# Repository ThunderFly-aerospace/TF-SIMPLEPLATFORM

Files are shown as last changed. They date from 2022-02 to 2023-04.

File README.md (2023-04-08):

# TF-SIMPLEPLATFORM - UAV autogyro takeoff platform

Device for launching unmanned drones (especialy autogyro type) from moving platforms (e.g. automobile roof).

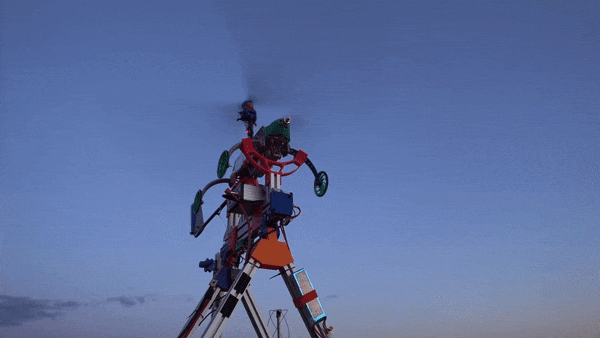
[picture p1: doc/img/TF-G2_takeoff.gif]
TF-SIMPLEPLATFORM with TF-G2 takeoff


The TF-SIMPLEPLATFORM is designed for launching of the unmanned [autogyro TF-G2](https://github.com/ThunderFly-aerospace/TF-G2/). Thanks to the combination of the this starting platform and the automatic takeoff mode of the TF-G2 unmanned autogyro, it is possible to perform safe and almost unattended takeoff. Platform is controlled from GCS based on realtime data from the UAV trough data-link. The platform can be disconnected manually (by operator) due to service operations.

The goal of the platform and automatic takeoff solution is to maximize the simplicity of the takeoff process and protect drone operators from external influences, such as adverse weather conditions.

## Parameters

| Parameter | Value | Note |
|---|---|---|
| Platform type | Rigid mount | Aluminium profiles design |
| Actuator| Clamps | |
| Manual override | Button on platform | |
| Remote control interface | USB/RS232 | |
| Operator takeoff confirmation | Yes, remote button | Wired controller |
| Control Software | Firmware, Mavlink interface in GCS | |
| Supported UAVs | [ThunderFly TF-G2](https://github.com/ThunderFly-aerospace/TF-G2) | |
| Supported flight stack | PX4 | (MavLink protcol) |

## Clamps mount mechanism
ezgif com-gif-maker

## Usage
  1. Prepare all required equipment. Check if it is properly mounted and connected. 
  1. ARM the autogyro, check all avionics. 
  2. Push the trigger switch to releas rotor holder. 
  3. Run by car few tens of meters
  4. Autogyro will takeoff automatically from roof. 

### Installation
The first step is to assemble the platform onto the movable platform. The standard method of assembly involves inserting it into plastic parts and securing it with a screw. It is important to tight the screw with the correct torque to prevent spontaneous loosening of the screw. 

### Wiring 
After mounting the platform, it is necessary to correctly connect it. The outdoor part is connected with the inner box using a cable terminated on both ends with the same 12-pin connector. This cable provides both power and data communication for the platform. 

## Description of control elements
The platform is equipped with a variety of actuators, sensors, control elements and visualization components. 

### Actuators
 - Servo motor for rotor holder
 - Servo motor for clamp

### Sensors 
 - Sensor of drone presence (in future version)

### Control elements
 - Button on platform itself - Restart button
 - Botton on platform itself - Open clamp
 - Button on wired controller - Permission for takeoff
 - External input for breake signal

### Visualization elements
 - 2 LEDS on platform (Platform status) 
 - 1 Loud buzzer on platform (Release status)
 - 2 LEDS on wired controller (Platform status)
 - 1 Buzzen on wired controller (Release status)

### Platform control 
The platform is typically controlled from a ground-station via USB or RS232. The platform is connected to the ground control station either through the USB port from internal box of the platform or directly through RS232. Once properly connected, it should be possible to communicate with the platform via a serial interface.

The ground stations from ThunderFly company are equipped with [software](https://github.com/ThunderFly-aerospace/TF-R1/blob/master/scripts/release_platform/release_platform_serial.py) that is capable of controlling the platform based on data obtained from the drone through the MAVLink network.

## Technical images 
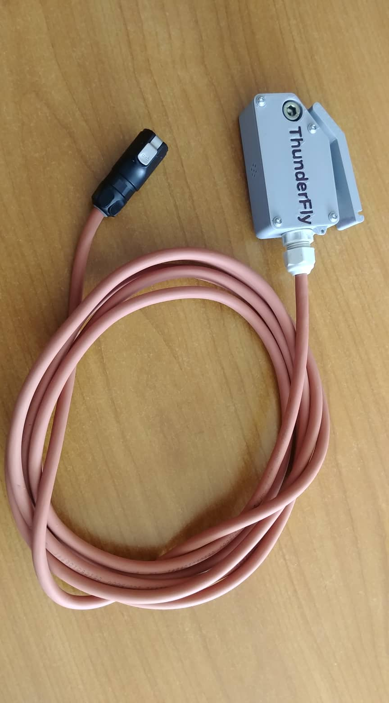
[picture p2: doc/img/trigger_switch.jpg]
TF-SIMPLEPLATFORM trigger switch

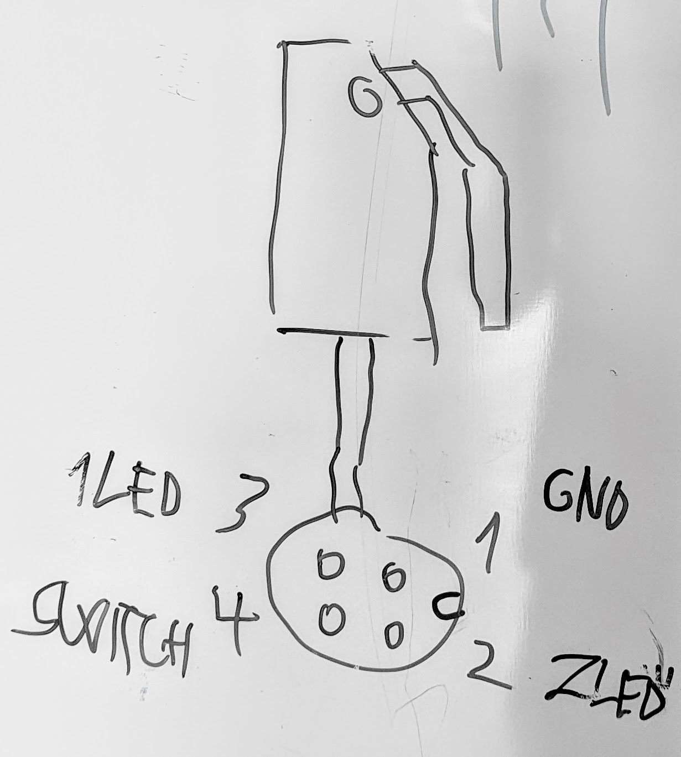
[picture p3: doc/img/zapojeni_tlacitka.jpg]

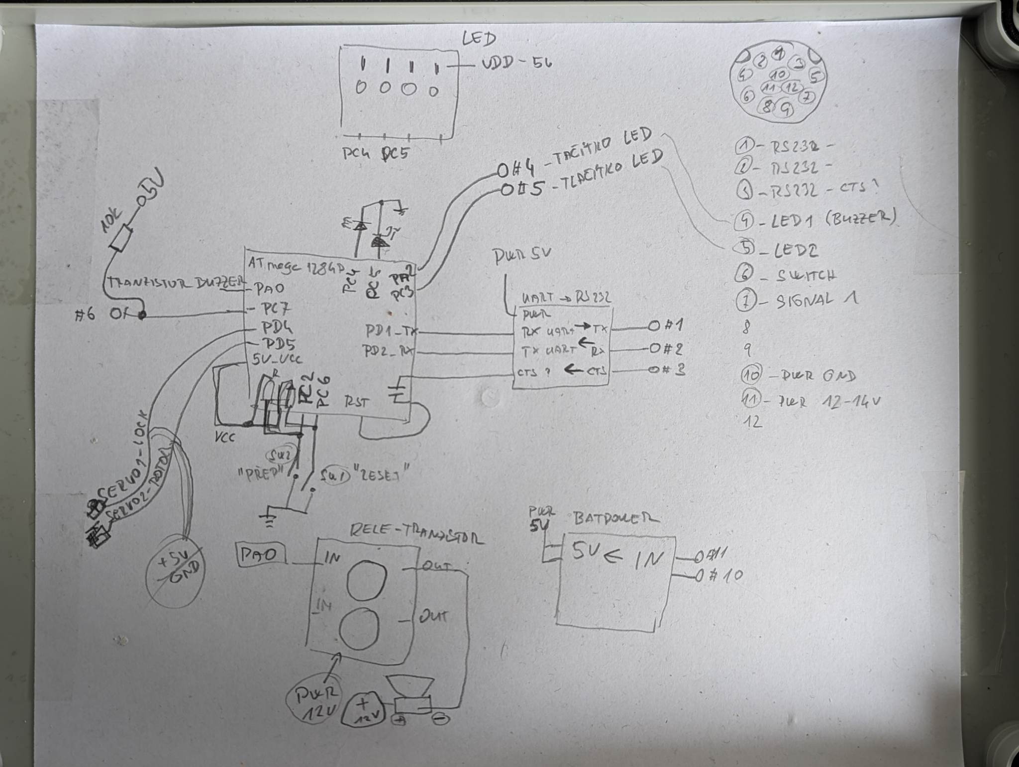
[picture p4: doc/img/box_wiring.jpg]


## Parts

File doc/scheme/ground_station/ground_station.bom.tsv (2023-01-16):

Id | Description | Qty | Unit | Designators
1 | Cable, 2 wires | 0 | m
2 | Cable, 3 wires | 0 | m
3 | Cable, 4 wires | 0 | m
4 | Connector, 20A | 1 |  | Power_Connector
5 | Connector, Ground Station Power | 1 |  | Main_Power
6 | Connector, MLAB RS232SINGLE01A | 1 |  | RS232
7 | Connector, MLAB USB232R02A | 1 |  | USB
8 | Connector, USB-A | 1 |  | MOX

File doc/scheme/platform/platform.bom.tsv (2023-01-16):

Id | Description | Qty | Unit | Designators
1 | Cable, 10 wires | 0 | m
2 | Cable, 2 wires | 0 | m
3 | Cable, 8 wires | 0 | m
4 | Cable, 9 wires | 0 | m
5 | Connector | 4 |  | Confirm_Btn_Connector, Platform_LED_1, Platform_LED_2, Servo_Connector
6 | Connector, 20A | 1 |  | Power_Connector
7 | Connector, GQ12B-10/R/A | 2 |  | Reset_Button, Rotor_Button
8 | Connector, MLAB ATmegaTQ4401A | 1 |  | Arduino
9 | Connector, MLAB BATPOWER04C | 1 |  | Power_Module
10 | Connector, MLAB NFET4X01B | 1 |  | NFET
11 | Connector, MLAB RS232SINGLE01A | 1 |  | RS232
12 | Connector, SC235 AF | 1 |  | Buzzer

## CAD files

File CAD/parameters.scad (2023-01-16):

maximum_printable_size = 150;

layer_thickness = 0.3;
global_clearance = 0.5;


//Screw diameter and nut for M10 [mm]
M10_screw_diameter = 10.4;
M10_head_height = 10;
M10_head_diameter = 16+0.5;
M10_nut_height = 10.5;
M10_nut_diameter = 25.5;
M10_nut_pocket = 22.3;

//Screw diameter for M8 [mm]
M8_screw_diameter = 8.6;
M8_head_height = 8;
M8_head_diameter = 13.5;
M8_nut_height = 7.5;
M8_square_nut_thin_height = 4.5;
M8_nut_diameter = 14.4 + 0.5;
M8_nut_pocket = 13 + 0.5;
M8_washer_diameter = 16;
M8_washer_thickness = 1.5;


//Screw diameter and nut for M6 [mm]
M6_screw_diameter=6.5;
M6_head_diameter = 10+0.5;
M6_head_height = 6;
M6_nut_height = 4.9;
M6_nut_diameter = 11.8;
M6_nut_pocket = 10.4;
M6_square_nut_height = 3;
M6_square_nut_diameter = 10;
M6_washer_thickness = 1.6;

//Screw diameter and nut for M5 [mm]
M5_screw_diameter=5.5;
M5_head_height = 5;
M5_head_diameter = 13+0.5;
M5_nut_height = 4.5;
M5_nut_diameter = 9.4;
M5_nut_pocket = 8.4;

//Screw diameter and nut for M4 [mm]
M4_screw_diameter=4.5;
M4_screw_head_height = 4;
M4_nut_height = 3.2;
M4_nut_diameter = 8.4;
M4_nut_pocket = 7.5;

//Screw diameter and nut for M3 [mm]
M3_screw_diameter = 3.2;
M3_nut_height = 2.7;
M3_nut_diameter = 6.6;
M3_nut_pocket = 5.6;
M3_screw_head_height = 3;

//Screw diameter and nut for M2,5 [mm]
M2_5_screw_diameter = 2.7;
M2_5_nut_height = 2.3;
M2_5_nut_diameter = 6;
M2_5_nut_pocket = 5.5;

//ALU profile
ALU_profile_width = 30.5;
ALU_profile_holder_wall_thickness = 3;
ALU_profile_groove_width = 8;





// Platform parameters ////////////////////////////////////////////
// Main profile parameters
starting_platform_length = 1000; // Main platform profile length
starting_platform_angle = 10; // Angle of attack for platform

// Main cube profile lengths
profile_length_x = 600;
profile_length_y = 600;
profile_length_z = 260;


// Compressor dimensions
compressor_length_x = 410;
compressor_length_y = 140;
compressor_length_z = 310;

// Platform front support parameters
front_holder_width = 160;
front_holder_angle = 25;
front_holder_height = 60;
front_holder_offset = 15;
front_holder_height_offset = 110;

// Lock moving servo parameters
// static par.
servo_length = 40;
servo_width = 20;
servo_height = 40;
servo_axle_offset = 12.5;
servo_axle_height = 5;
servo_movement_angle = 60;
servo_movement_angle_offset = -35; // angle offset up
servo_force = 1.65; // [N/m] torque of servo

// dynamic par.
servo_arm_length = servo_width/2+ALU_profile_width/2+ALU_profile_holder_wall_thickness+4;
servo_travel_y = cos((servo_movement_angle-abs(servo_movement_angle_offset))/2)*servo_arm_length;
servo_arm_hole_length = (servo_arm_length/cos(servo_movement_angle/2))-servo_arm_length+M3_screw_diameter;
servo_joint_offset = sin(servo_movement_angle+servo_movement_angle_offset)*(servo_arm_length+servo_arm_hole_length)+servo_axle_offset;
servo_joint_offset_by_angle = -tan(servo_movement_angle_offset)*servo_arm_length;
servo_max_linear_force = servo_force/(servo_arm_length/1000); // max servo linear force [N]
servo_min_linear_force = cos(servo_movement_angle+abs(servo_movement_angle_offset))*servo_max_linear_force; // min servo linear force [N] in the most extreme position
servo_holding_linear_force = cos(servo_movement_angle+servo_movement_angle_offset)*servo_max_linear_force; // min servo linear force [N] in holding position

// Lock static parameters
lock_screws_dia = 3.2;
lock_depth = 20;
lock_axle_diameter = 15;
lock_grab_axle_dia = 13;
lock_arms_joint_offset = 30;
lock_arms_joint_angle = 90-.01;
lock_tooth_width = 2;

lock_tube_angle = 0;

// Lock dynamic parameters
lock_push_force = (servo_holding_linear_force/cos(lock_arms_joint_angle))/cos(lock_arms_joint_angle); // lock arm pushing force on linear servo joint
lock_push_arm_length = 45;
lock_arm_force_ratio = 1; // lock arm change holding force ratio (0.5 = arm will have half holding force)
lock_hold_arm_length = lock_push_arm_length/lock_arm_force_ratio;
lock_holding_force = lock_push_force*lock_arm_force_ratio;
lock_joint_arm_length = lock_push_arm_length;

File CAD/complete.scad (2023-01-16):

include <./parameters.scad>
use <./src/lib/ALU_profile.scad>

use <./src/888_1010.scad> // not used

use <./src/assembly/cube_box.scad>
use <./src/assembly/platform.scad>


// Measuring box
main_box();

// Platform
translate([-22, 0, profile_length_z-ALU_profile_width/2+2])
rotate([0, -starting_platform_angle, 180])
platform();

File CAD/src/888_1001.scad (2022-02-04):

include <../parameters.scad>
use <./lib/ALU_profile_holder_top.scad>



module 888_1001() {
	translate([0, 35.01, 0])
	difference() {
		union() {
			hull() {
				cube([ALU_profile_width+ALU_profile_holder_wall_thickness*2, 5, ALU_profile_width]);

				translate([ALU_profile_width+ALU_profile_holder_wall_thickness*2+8, 70, 0])
				cylinder(d=5, h=ALU_profile_width/2, $fn=30);

				translate([-8, 70, 0])
				cylinder(d=5, h=ALU_profile_width/2, $fn=30);
			}

			translate([0, -35.01, 0])
			ALU_profile_holder_top();
		}
		

		// tube hole
		translate([0, 0, -1])
		hull() {
			translate([ALU_profile_width/2+ALU_profile_holder_wall_thickness, 60, 0])
			cylinder(d=lock_grab_axle_dia, h=ALU_profile_width+2, $fn=30);

			translate([ALU_profile_width+ALU_profile_holder_wall_thickness*2+8, 80, 0])
			cylinder(d=lock_grab_axle_dia, h=ALU_profile_width+2, $fn=30);

			translate([-8, 80, 0])
			cylinder(d=lock_grab_axle_dia, h=ALU_profile_width+2, $fn=30);
		}

		// middle body hole
		translate([0, 0, -1])
		hull() {
			translate([ALU_profile_width/2+ALU_profile_holder_wall_thickness-8, 15, 0])
			cylinder(d=lock_grab_axle_dia, h=ALU_profile_width+2, $fn=30);

			translate([ALU_profile_width/2+ALU_profile_holder_wall_thickness-10, 15, 0])
			cylinder(d=lock_grab_axle_dia, h=ALU_profile_width+2, $fn=30);

			translate([ALU_profile_width/2+ALU_profile_holder_wall_thickness-8, 40, 0])
			cylinder(d=lock_grab_axle_dia, h=ALU_profile_width+2, $fn=30);

			translate([2, 50, 0])

			cylinder(d=lock_grab_axle_dia, h=ALU_profile_width+2, $fn=30);
		}

		mirror([1, 0, 0])
		translate([-ALU_profile_width-ALU_profile_holder_wall_thickness*2, 0, -1])
		hull() {
			translate([ALU_profile_width/2+ALU_profile_holder_wall_thickness-8, 15, 0])
			cylinder(d=lock_grab_axle_dia, h=ALU_profile_width+2, $fn=30);

			translate([ALU_profile_width/2+ALU_profile_holder_wall_thickness-10, 15, 0])
			cylinder(d=lock_grab_axle_dia, h=ALU_profile_width+2, $fn=30);

			translate([ALU_profile_width/2+ALU_profile_holder_wall_thickness-8, 40, 0])
			cylinder(d=lock_grab_axle_dia, h=ALU_profile_width+2, $fn=30);

			translate([2, 50, 0])
			cylinder(d=lock_grab_axle_dia, h=ALU_profile_width+2, $fn=30);
		}
	}
}

888_1001();

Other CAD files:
CAD/src/888_1002.scad
CAD/src/888_1003.scad
CAD/src/888_1004.scad
CAD/src/888_1005.scad
CAD/src/888_1006.scad
CAD/src/888_1007.scad
CAD/src/888_1008.scad
CAD/src/888_1009.scad
CAD/src/888_1010.scad
CAD/src/888_1011.scad
CAD/src/888_1012.scad
CAD/src/888_1013.scad
CAD/src/888_1014.scad
CAD/src/888_1015.scad
CAD/src/888_1016.scad
CAD/src/888_2001.scad
CAD/src/888_2002.scad
CAD/src/888_2003.scad
CAD/src/888_2004.scad
CAD/src/888_2005.scad
CAD/src/888_3001.scad
CAD/src/888_3002.scad
CAD/src/888_3003.scad
CAD/src/888_3004.scad
CAD/src/888_3005.scad
CAD/src/888_3006.scad
CAD/src/888_3007.scad
CAD/src/assembly/cube_box.scad
CAD/src/assembly/front_support.scad
CAD/src/assembly/lock.scad
CAD/src/assembly/platform.scad
CAD/src/assembly/rotor_lock.scad
CAD/src/printplate/888_1001_printplate.scad
CAD/src/printplate/888_1002_printplate.scad
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

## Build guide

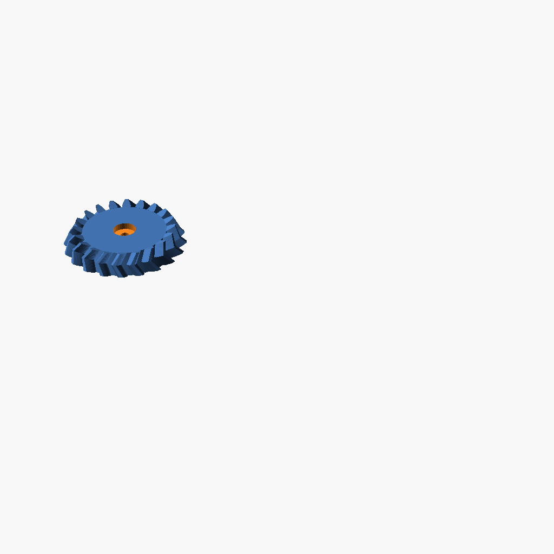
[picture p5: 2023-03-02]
CAD/png/888_3003_printplate.png

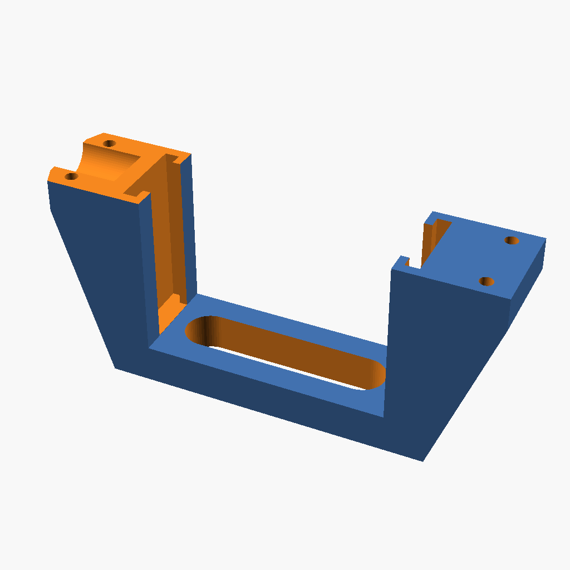
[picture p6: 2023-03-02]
CAD/png/888_3006_printplate.png

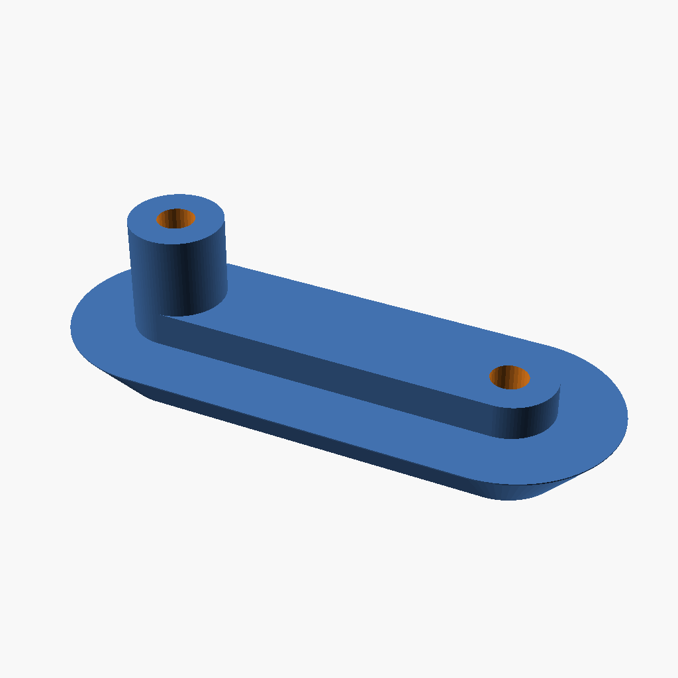
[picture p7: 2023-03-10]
CAD/png/888_1004_printplate.png

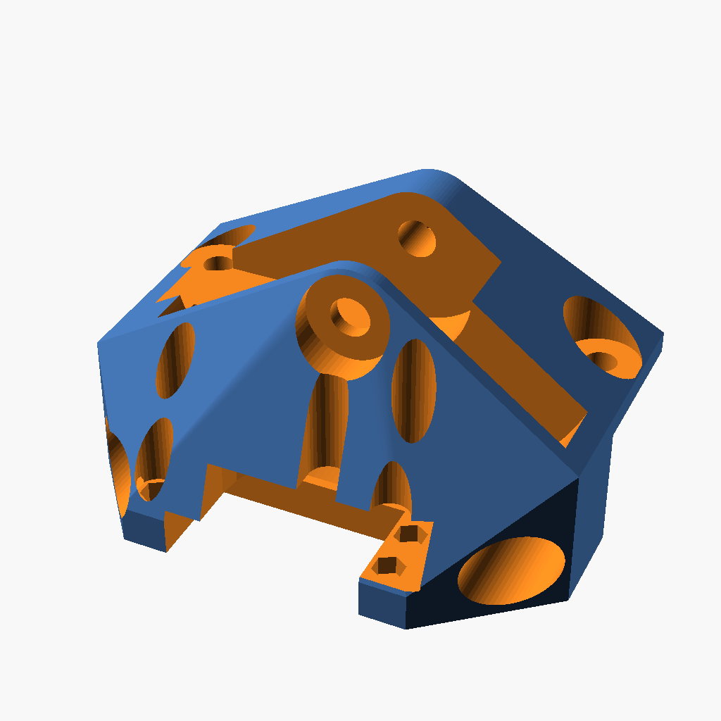
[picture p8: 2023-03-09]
CAD/png/888_3001_printplate.png

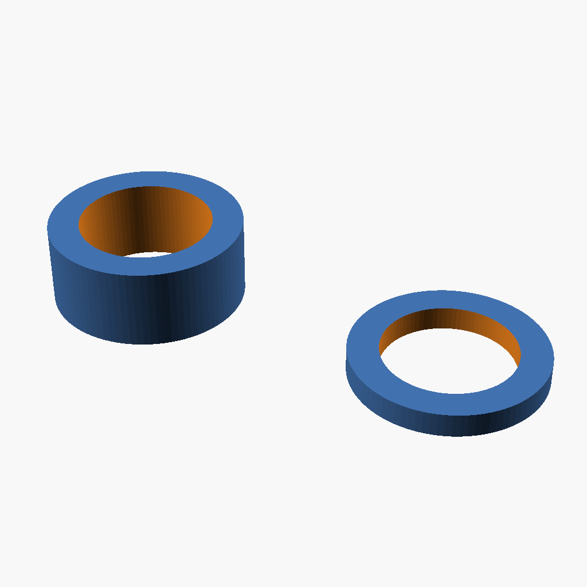
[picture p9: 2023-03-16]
CAD/png/888_3007_printplate.png

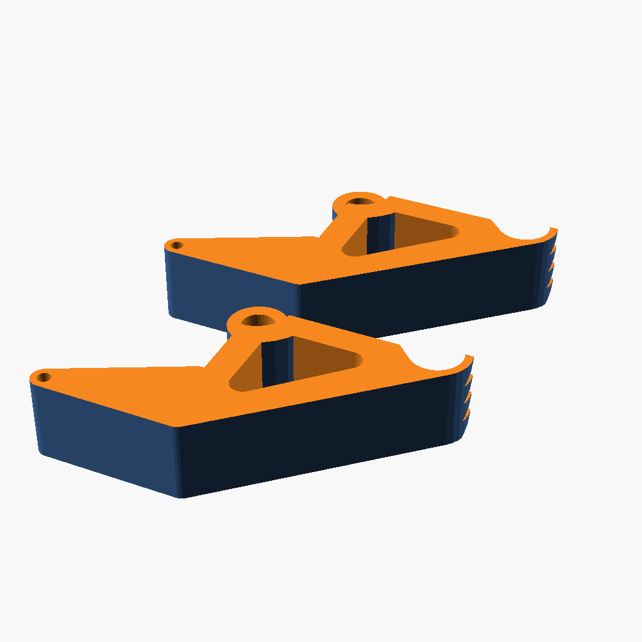
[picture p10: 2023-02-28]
CAD/png/888_1005_AB_printplate.png

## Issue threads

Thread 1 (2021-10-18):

Elektromechanické řešení odpojování vírníku

kaklik, 2021-10-18:
Návrh od @taury55
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

Možnosti odpojovacích zámků:
- https://www.gme.cz/elektromagneticke-zamky?
- https://dratek.cz/8806-tazne-elektromagnety/#sc=342

kaklik, 2021-10-18:
Vzhledem k tomu, že se ukazuje jako komplikované vyřešit prostup pro zámek skrz pláštěnku na trupu. Tak jsme dnes s @roman-dvorak  vymysleli řešení, kdy by vírník byl uchycen pouze za vnější části mimo pláštěnku. Konkrétně za ocasní trubku a podvozkové nohy.

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

Čtvrtý bod uchycení by bylo místo ze kterého se bude odpojovat zámek.  Výhodou tohoto řešení je fakt, že pak stačí pouze jeden akční člen k uchycení vírníku.

taury55, 2021-11-02:
První náhled na novou platformu vypadá takto. (Zatím jsou jen pasivní prvky)

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

Zjistil jsem že 400mm, které používá TF-MOTORSCALE je celkem těsné/stísněné pro platformu TF-G2. trochu uvažuji o vynechání zadní podpory a pouze nechat zámek.

roman-dvorak, 2021-11-02:
To vypadá zajímavě. Ty Učka, co drží podvozkové nohy (i ocasní tyč) jsem si představoval o dost mělčí.

Nešlo by tu zadní podpěru celotištěnou?

Myslím, že váze nevadí, že profil bude trochu protažený dopředu.

taury55, 2021-11-02:
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

Mělčí samozrejmě není problém.

Myslíš jako nepoužít ten ALU profil? Jestli ano, tak jsem ho použil, protože máme dost takhle malých zbytků a mám díky tomu nějakou pevnost navíc bez kreslení.

Nevadí mít profil více dopředu, ale použil jsem délku, která je aktuálně na TF-MOTORSCALE, takže bychom museli udělat nový.

kaklik, 2021-11-02:
>
> Zjistil jsem že 400mm, které používá TF-MOTORSCALE je celkem těsné/stísněné pro platformu TF-G2. trochu uvažuji o vynechání zadní podpory a pouze nechat zámek.

Ten návrh vypadá dost designově. :D
Myslím si, že není možné vynechat zadní podporu a použít pouze zámek, protože záklon vírníku drží podpora v kombinaci se zámkem.
Pokud je nutné použít delší profil, tak bych spíše navrhoval na motorovou váhu připevnit další profil na ten, který tam aktuálně je.

roman-dvorak, 2021-11-02:
> Myslíš jako nepoužít ten ALU profil? Jestli ano, tak jsem ho použil, protože máme dost takhle malých zbytků a mám díky tomu nějakou pevnost navíc bez kreslení.

Ano, úplně zbytečně to pak zesložiťuje další výrobu a dalši skládání. Je tam zbytečný spoj navíc.

taury55, 2021-11-02:
Takto by zhruba vypadal zámek se solenoidem. Je nutné aby solenoid měl délku posunu alespoň 15mm, aby se čelisti rozevřeli, co nejvíce. Na obrázku je rozevření čelistí přibližně, pokud by byl posun přesně na 15mm. Jako referenci jsem používal tento solenoid, který má posun kolem 15-20mm. https://www.tme.eu/en/details/282367-024/solenoids/saia-burgess/
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

roman-dvorak, 2021-11-02:
Délka posuvu X rozevření kleští lze ovlivnit tím, jak daleo od osy rozevírání kleští bude táhlo ukotveno. To však bude ovlivňovat výslednou sílu rozevření. Je proto potřeba najít nějaké optimum, protože i magnet s délkou výsuvu ztrácí sílu.

taury55, 2021-11-02:
Jo, to si uvědomuju. Ale zjistil jsem, že solenoidy je problém sehnat s delším posuvem. Ale s větší sílou není.

Dodělal jsem to jako gif, který počítá to nahnutí v závislosti na posunu solenoidu. Zanedbávám to, že tahám lineárně za ten úchytný bod, ale to už by neměl být téměř žádný rozdíl.

taury55, 2021-11-21:
Takto bych si nyní představoval zámek. Zvolil jsem nakonec servo (D485HW) z těchto důvodů:

- Solenoidy se pro naše požadované síly dělají velmi málo a dokonce je potřeba použít větší výkon než, který dokáží trvale uchladit.
- Solenoidy, které by potencionálně mohli být na našem zámku jsou beze pružiny. Proto je nutné použit pro vracení/držení v zamknuté poloze nezávislá pružina, což komplikuje konstrukci a sestavení zámku.
- Solenoidy ztrácí sílu exponenciálně, takže mají velmi omezený rozsah pohybu, což zveličuje dva ostatní faktory.

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
Graf síly, kterou může působit na různé vzdálenosti jeden z nejsilnějších solenoidů, které jsem našel a chtěl použít.

Takto by zámek fungoval.
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

kaklik, 2021-11-21:
Ok, to vypadá dobře. :)  Ten mechanismus by to asi chtělo zkusit vyrobit v nějaké základní verzi a vyzkoušet na trubce s generátorem signálu pro serva.

Pak ale vznikla ještě otázka jakým způsobem budeme ovládat to servo? Přidáme k tomu nějaký arduino?

roman-dvorak, 2021-11-21:
Jo, bylo by fajn k tomu přidat arduino s tlačítkem, LEDkou a USB sériovkou. Přes kterou by to dostávalo příkaz z pythonu.

taury55, 2021-11-29:
Zatím pouze testování zda a co funguje, ale pomalinku bychom mohli mít první prototyp.

Tady jsem upravil trochu geometrii a přidal jsem číslo pro animaci, které zobrazuje aktuální rozevření čelistí.
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

slimonslimon, 2021-11-29:
zvědavý dotaz, vůbec nesouvisející s tématem: Jak děláš ty animace?

taury55, 2021-11-29:
Je to strašně jednoduché. Stačí přidat proměnou `$t` a ta se mění z 0 na 1 v závislosti na čase animace.
Poté se v OpenSCADu v menu "view" zaškrtne políčko "animate", které zapína menu pro volbu FPS a počtu snímků.
Poslední iterace jsem udělal pomocí cosínu, aby docílil toho jemného přechodu.
[https://www.instructables.com/Animating-with-OpenSCAD/](Instructables - Návod na animace v OpenSCADu)

taury55, 2021-11-29:
Mechanismus zámku poprvé otestován v realném světě.
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

Testování síly serva na držení tyčky:
https://user-images.githubusercontent.com/33667517/143953920-2548221a-6896-4648-88ac-2952e82de2f8.mp4

Projevil se problém s tolerancema, které jsem upravoval. První výtisk měl až moc velký odpor. A tak jsem zvedl tolerance děr a tím vznikl nepříjemný "backslash" (nevím jak je to v češtině...), který je potřeba do další verze opravit. Jinak vypadá zámek funkčně a připraven na první testování. Také je možno vidět, že servo utíká. Není připevněno na pevno, protože nemám doma M2.5 šrouby a hlavně matice a také tím servo nemohu zníčit.
https://user-images.githubusercontent.com/33667517/143954089-8f5fc323-e213-4be6-abc5-6170f31f755c.mp4

roman-dvorak, 2021-12-06:
Možná by bylo vhodné, aby se ty kleštiny v zavřeném stavu neopíraly o sebe. Aby mezi nimi byla malá mezera a domáčklo se to k trubce ocasu. Možná by se tam mohla vlepit nějaká tenká guma (např. z duše od kola).

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
Aby v (především) vyznačených místech byla nějaká mezera. V zavřeném stavu.

taury55, 2021-12-06:
Zatím jsem tiskl dvě varianty čelistí. Obě neměli problém s držením trubky, ale trubka měla volnost ve svojí ose, takže mohla rotovat v ose letu. Tak nevím jestli je to žádané nebo ne. Takže to nevidím jako nutné. Spíše, jestli chceme držet ve všech osách nebo v zámku bude tato osa volná a bude držet pomocí těch podpor.

Tomu pohybu, co aktuálně stejně v zámku moc zabránit, protože, když se tam dá např guma, tak bude všechna síla v té ose pusobit pouze na tu gumu a snažit se jí vyrvat.

taury55, 2021-12-08:
Myslím, že mechanická část je hotová.
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

slimonslimon, 2021-12-08:
Vypadá to cool.

Jak dobře to jde ta trubka vypáčit?

(teď tě čeká ta softwarová... upřímnou soustrast)

taury55, 2021-12-08:
Pokud ji člověk nechce vytáhnout, tak se člověk musí dost snažit. Kombinace 50 N a té geometrie je úplně dostatečná. A v realitě to pocitově celkem odpovídá, že ta síla taková.

@kaklik @roman-dvorak Co se týče ovládání, tak bych tam dal ESP32, které by se automaticky připojovalo na wifi auta. Reagovalo na naarmování a pokyn pro vypuštění. Co si o tom myslíte?

roman-dvorak, 2021-12-08:
Super, tohle vypadá hezky a dost použitelně!

Co se týče ovládání, popsal jsem to do vlastního issue: https://github.com/ThunderFly-aerospace/Simple-platform/issues/3

roman-dvorak, 2021-12-08:
Ještě tedy je potřeba domodelovat ty zbylé dvě podpěry.

kaklik, 2022-02-08:
Tohle považuji za hotové. Potenciálním vylepšením je vytvoření asymetrických podpěr pod přední podvozkové nohy, aby vírník z podpěr nemohl vypadnout směrem dozadu.  Nemyslím si ale že je to v případě použití vírníku s nepopraskanou podložkou nějaký problém.

Closed 2022-02-08.

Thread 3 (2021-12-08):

Řídící elektronika  a software pro řízení odpojovací platformy

roman-dvorak, 2021-12-08:
Řídící elektronika by měla být založena na arduinu, kterému se budou posílat příkazy po sériovce.

V krabičce u odpojovacího zařízení by mělo být:
 * [x] Arduino (Labduino) (procesor ATmega328P)
 * [x] převodník USB-UART
 * [x] Měnič z 12-18V na 5V (možnost napájení z auta tak i z LI-pol akumulátoru
 * [x] Servo HUB s pro napájení z měniče
 * [x] Tlačítko na manuální otevření zámku (v čělíčku krabičky)  - V čelíčku by mohl být MIC (3pin) konektor.
 * [x] Vzdálené tlačítko pro potvrzení odpojení.
   * [x] Vytvořit tištěný grip pro [potvrzovací tlačítko](https://github.com/ThunderFly-aerospace/TF-SIMPLEPLATFORM/issues/4)
   * [X] Indikační LED pro zobazení stavu platformy (více stavů než otevřeno zavřeno)
 * [x] LED indikace otevření zámku (v čelíčku krabičky)
 * [x] Hliníkova karbička + odpovdající ALBASE (pokud se to vejde do malé, tak by asi byla vhodnější)

Arduino by mělo o sobě po celou dobu dávat vědět. I s tím, v jakém je stavu. Takže napřiklad 2x za sekundu po sériovce pošle že žije (číslo zprávy,  že se nerestartoval) a aktuální stav zámku, stav povolovacího tlačítka.

Bylo by fajn mit z arduina vyvedený jeden signál, který bude říkat stav zámku. Bude na něj možné připojit nějakou sirénku, nebo svetelnou indikaci.

Arduino po sériovce zároveň bude přijímat příkazy. Takové příkazy budou:
 * Otevřít zámek?
 * Zavřít zámek?
 * Jaký je stav systému?

## Zpráva z arduina do GCS:
```
$S;<cislo zpravy int>;<stav tlačítka pro otevření int1>;<stav tlačítka pro povolení startu int1>;<logická poloha zámku int1>;<poloha serva int>;<blokace_otevreni int1>;\n
```
## Zprávy z GCS do arduina:

### Otevřít zámek:
```
$O;<delka otevreni int8>;<vyžadovat potvrzení int1>;\n
```
`delka otevreni` [s] - nula znamená nestarat se o délku otevření, jinou hodnotu zatím nebudeme používat.
`vyžadovat potvrzení` - Odpojit pouze v případě stisknutého potvrzovacího tlačítka - zatím není nutné implementovat.

### Zablokovat otevření
```
$BL;\n
```
Tímto se zablokuje otevření manuálním tlačítkem. Toto se využije pro nechtěné otevření například za jízdy auta. Manuální otevření se zablokuje po naarmování autopilota. Zamek tak půjde otevřít pouze příkazem po sériovce a se stisknutým ready tlačítkem.

### Odlokovat otevření
```
$UL;\n
```
Odblokování tlačítka pro manuální otevření

### Zavrit zamek:
```
$C;\n
```

### Ziskat stav:
```
$GS;\n
```
Odpovedi by mela byt zprava se stavem

## Logika ovládání:

Tlačítko pro manuální odpojení - Po dobu stisknutého tlačítka nechat otevřený zámek
Signál pro otevření po sériovce - Zámek otevřít pouze v případě stisknutného tlačítka. Nechat otevřené
Signál pro zavření po sériovce - Zavřít zámek vždy

roman-dvorak, 2022-01-16:
@taury55 v první iteraci stačí vyřešit:
- [ ] aby se zámek otevřel na příkaz po sériovce při stisknutém "READY" tlačítku.
- [ ] Při stisknutí tlačítka "OPEN" (na krabičce) otevřít zámek
- [ ] Periodicky posílat informaci o stavu

Zbytek (zprávy o stavu platformy) budeme řešit později

kaklik, 2022-01-28:
Z elektroniky, kterou @roman-dvorak  přivezl do hangáru, jsem sestavil [LABduino](https://wiki.mlab.cz/doku.php?id=cs:labduino#pripojeni_na_usb) a nahrál do něj bootloader pro Arduino Duemilanove.
Nyní je elektronika v tomhle stavu:

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

Zároveň je v arduinu nahrán "Blink example".  Myslím, že je v hangáru možná nedostatek MLAB propojovacích drátků.  Určitě chybí dvojlinka pro připojení vzdáleného tlačítka.

kaklik, 2022-02-06:
@taury55 Přivezl jsem ze Soběslavi kulatou dvoulinku se silikonovou izolací. Myslím že je to vhodný kabel pro připojení vzdáleného [odpojovacího tlačítka](#4 ).

kaklik, 2022-03-03:
Myslím, že sučasná elekronika a firmware naplňuje základní funkčnost popsanou v tomto issue.

kaklik, 2022-05-12:
Ještě je potřeba k platformě doplinit výkonové spínací moduly [na pípák](https://www.mlab.cz/module/REL1SW01A) a [pro maják](https://www.mlab.cz/module/NFET4X01B).   @ChroustJan  myslíš, že bys to mohl zajistit?

ChroustJan, 2022-06-16:
@kaklik je to stále aktuální?

kaklik, 2022-06-16:
> @kaklik je to stále aktuální?

nepoznám z toho na co konkrétně se ptáš, ale odhaduju že na ty výkonové spínací moduly. Já zatím našel akorát jeden [tenhle](https://www.mlab.cz/module/NFET4X01B)  a vzhledem k tomu, že těch platforem potřebujeme více a zároveň je aktualizovat, tak ano, myslím si, že je to stále aktuální.

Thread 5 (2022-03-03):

Úpravy před změnou na pneumatické ovládání

kaklik, 2022-03-03:
- [ ] Nová verze potvrzovacího tlačítka,
- [ ] Zvuková signalizace
- [ ] Přetisknout zámek na větší servo a zmenšit tolerance.
- [ ] Zlepšit parser na zprávy a doladit komunikační logiku.
- [ ] Případně upravit závěs předního podvozku.

taury55, 2022-03-04:
Fotografie nového confirm buttonu pro platformu.

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

Nově přidané asymetrické úchyty na přední podvozek vírníku TF-G2.

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

taury55, 2022-03-07:
@kaklik Co znamená dát krabičku obráceně? Jako otočit, aby směřovali signálky na levou místo pravou nebo úplně nové umístění?

roman-dvorak, 2022-03-07:
To předpokládám, že vychází ze zápisu, kam jsem tohle navrhoval já.

A ano, bylo to myšleno otočit krabičku tak, aby (hlavně) kabely směřovaly na levou stranu. A to z důvodu, aby kabely vedly skrze dveře, které se (a budou se) využívat co nejméně. A kam se bude co nejméně nastupovat.

kaklik, 2022-04-19:
Pro vyřešení zvukové signalizace je potřeba přidat modul s tranzistorem.  Zřejmě [RELSW](https://www.mlab.cz/module/REL1SW01A) nebo [NFET4X01B](https://www.mlab.cz/module/NFET4X01B), který by pak šel použít i pro případné spínání pneumatických solenoidů.

roman-dvorak, 2022-04-19:
Podstatným aspektem je zde velkiost modulu, protože se aktuálně používá malá al krabička.

NFET modul je hodně velký. RELSW by se možná mohl vejít. @taury55?

taury55, 2022-04-20:
> Podstatným aspektem je zde velkiost modulu, protože se aktuálně používá malá al krabička.
>
> NFET modul je hodně velký. RELSW by se možná mohl vejít. @taury55?

Já jsem tam předskládal moduly a nyní je tam celkem dost místa, takže by se tam měli jakýkoliv z modulů jednoduše vejít.

kaklik, 2022-07-18:
Myslím že všechny zde zmíněné změny jsou nyní na platformě implementovány.

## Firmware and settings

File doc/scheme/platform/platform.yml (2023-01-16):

connectors:
  Power_Connector:
    type: 20A
    show_pincount: false
    pinlabels: [TxD, 12v, GND, RxD]
  RS232:
    type: MLAB RS232SINGLE01A
    show_pincount: false
    pinlabels: [GND, VCC, RxD(12v), TxD(12v), RxD(5v), TxD(5v)]
  Power_Module:
    type: MLAB BATPOWER04C
    show_pincount: false
    pinlabels: [GND, 12v, 5v]
  Arduino:
    type: MLAB ATmegaTQ4401A
    show_pincount: false
    pinlabels: [GND, VCC, RESET#, PA0, PA2, PC2, PC3, PC4, PC5, PC6, PC7, PD0, PD1, PD4, PD5]
  NFET:
    type: MLAB NFET4X01B
    show_pincount: false
    pinlabels: [GND, VCC, IN3, OUT3+, OUT3-]
  Buzzer:
    type: SC235 AF
    show_pincount: false
    pinlabels: [GND, VCC]
  Reset_Button:
    type: GQ12B-10/R/A
    show_pincount: false
    pincount: 2
  Rotor_Button:
    type: GQ12B-10/R/A
    show_pincount: false
    pincount: 2
  Platform_LED_1:
    show_pincount: false
    pincount: 2
    pinlabels: [GND, VCC]
  Platform_LED_2:
    show_pincount: false
    pincount: 2
    pinlabels: [GND, VCC]
  Servo_Connector:
    show_pincount: false
    pinlabels: [Rotor_Servo_SIG, GND, 5v, Lock_Servo_SIG]
  Confirm_Btn_Connector:
    show_pincount: false
    pinlabels: [GND, LED1+Buzzer, LED2, Btn]

cables:
  PW_1:
    show_name: false
    show_wirecount: false
    colors: [GY, GY, OG, OG, WH, GN, GY, OG, WH, GN]
  PW_2:
    show_name: false
    show_wirecount: false
    colors: [GY, OG]
  PW_3:
    show_name: false
    show_wirecount: false
    colors: [GY, OG, GN, OG, YE, WH, OG, GY, GN]
  PW_4:
    show_name: false
    show_wirecount: false
    colors: [GN, WH]
  PW_5:
    show_name: false
    show_wirecount: false
    colors: [BN, GN, BN, GN, WH, OG, WH, OG]

connections:
  -
    - Power_Connector: [2, 2, 3, 3]
    - PW_1: [1-4]
    - Power_Module: [1, 1, 2, 2]
  -
    - Power_Connector: [1, 4]
    - PW_1: [5-6]
    - RS232: [4, 3]
  -
    - Power_Module: [1, 3]
    - PW_2: [1-2]
    - RS232: [1, 2]
  -
    - Power_Module: [1, 3]
    - PW_2: [1-2]
    - NFET: [1, 2]
  -
    - RS232: [1, 2, 5, 6]
    - PW_3: [1, 2, 4, 5]
    - Arduino: [1, 2, 13, 12]
  -
    - NFET: [3]
    - PW_3: [3]
    - Arduino: [4]
  -
    - NFET: [5, 4]
    - PW_4: [1-2]
    - Buzzer: [1-2]
  -
    - Arduino: [1, 10]
    - PW_5: [1-2]
    - Reset_Button: [1-2]
  -
    - Arduino: [1, 6]
    - PW_5: [3-4]
    - Rotor_Button: [1-2]
  -
    - Arduino: [1, 8]
    - PW_5: [5-6]
    - Platform_LED_1: [1-2]
  -
    - Arduino: [1, 9]
    - PW_5: [7-8]
    - Platform_LED_2: [1-2]
  -
    - Servo_Connector: [2, 3]
    - PW_1: [7, 8]
    - Power_Module: [1, 2]
  -
    - Servo_Connector: [4, 1]
    - PW_1: [9, 10]
    - Arduino: [14, 15]
  -
    - Confirm_Btn_Connector: [1-4]
    - PW_3: [6-9]
    - Arduino: [1, 5, 7, 11]

tweak:
  override:
    graph:
      ranksep: "1"  # Reduce the horizontal spacing (default 2)
    PW_1: &hide_table
      shape: none  # Hide the surrounding frame
      fontsize: "0.1"  # Reduce the space needed for text
      fontcolor: white  # Same as background to hide the text
    PW_2:
      <<: *hide_table
    PW_3:
      <<: *hide_table
    PW_4:
      <<: *hide_table
    PW_5:
      <<: *hide_table

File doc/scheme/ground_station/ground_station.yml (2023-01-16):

connectors:
  MOX:
    type: USB-A
    show_pincount: false
    pinlabels: [GND, VCC, Data+, Data-]
  USB:
    type: MLAB USB232R02A
    show_pincount: false
    pinlabels: [GND, VCC, Data+, Data-, RxD, TxD]
  RS232:
    type: MLAB RS232SINGLE01A
    show_pincount: false
    pinlabels: [GND, VCC, RxD, TxD, RxD, TxD]
  Power_Connector:
    type: 20A
    show_pincount: false
    pinlabels: [GND, 12v, RxD, TxD]
  Main_Power:
    type: Ground Station Power
    show_pincount: false
    pinlabels: [GND, 12v]

cables:
  GSW_1:
    wirecount: 4
    show_name: false
    show_wirecount: false
    colors: [BK, RD, WH, GN]
  GSW_2:
    wirecount: 4
    show_name: false
    show_wirecount: false
    colors: [BK, RD, YE, GN]
  GSW_3:
    wirecount: 3
    show_name: false
    show_wirecount: false
    colors: [BK, YE, GN]
  GSW_4:
    wirecount: 2
    show_name: false
    show_wirecount: false
    colors: [BK, RD]

connections:
  -
    - MOX: [1-4]
    - GSW_1: [1-4]
    - USB: [1,2,4,3]

  -
    - USB: [1, 2, 5, 6]
    - GSW_2: [1, 2, 3, 4]
    - RS232: [1, 2, 3, 4]

  -
    - RS232: [1, 5, 6]
    - GSW_3: [1, 2, 3]
    - Power_Connector: [1, 3, 4]

  -
    - Main_Power: [1, 2]
    - GSW_4: [1, 2]
    - Power_Connector: [1, 2]

tweak:
  override:
    graph:
      ranksep: "1"  # Reduce the horizontal spacing (default 2)
    GSW_1:
      shape: none  # Hide the surrounding frame
      fontsize: "0.1"  # Reduce the space needed for text
      fontcolor: white  # Same as background to hide the text
    GSW_2:
      shape: none  # Hide the surrounding frame
      fontsize: "0.1"  # Reduce the space needed for text
      fontcolor: white  # Same as background to hide the text
    GSW_3:
      shape: none  # Hide the surrounding frame
      fontsize: "0.1"  # Reduce the space needed for text
      fontcolor: white  # Same as background to hide the text
    GSW_4:
      shape: none  # Hide the surrounding frame
      fontsize: "0.1"  # Reduce the space needed for text
      fontcolor: white  # Same as background to hide the text

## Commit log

2021-11-02 All passive holders done
    [888_1001.scad, 888_1002.scad, 888_1003.scad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]
2021-11-21 Servo lock construction added
    [888_1004.scad, 888_1005.scad, 888_1006.scad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]
2021-11-29 Geometry of the lock changed
    [888_1004_printplate.scad, 888_1005.scad, 888_1005_printplate.scad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]
2021-12-06 New math for servo
    [888_1005.scad, 888_1006.scad, 888_1007.scad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]
2021-12-07 888_1008 changed self tapping screws
    [888_1008.scad]
2022-02-04 Holders redesign to make fit with the lock
    [888_1001.scad, 888_1001_printplate.scad, 888_1002.scad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]
2022-02-21 Comfirmation button box added
    [888_1011.scad, 888_1012.scad, 888_1013.scad]
2022-02-24 HW box models added
    [888_1011.scad, 888_1012.scad, 888_1013.scad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]
2022-03-01 New backplate and functional FW for platform
    [888_1016.scad]
2022-03-03 new confirm button box
    [888_1011.scad, 888_1012.scad]
2022-03-03 asymetric leg supports added
    [888_1003.scad]
2022-03-04 crane joint added
    [888_1016.scad]
2022-03-07 Platform hook reinforced
    [888_1016.scad]
2022-03-23 lock movement redesign with holding feature
    [888_1004.scad, 888_1005.scad, 888_1008.scad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]
2022-04-06 fixed tolerance for 888_1004
    [888_1004.scad]
2022-04-06 adding hole for buzzer
    [888_1015.scad]
2022-05-08 servo control improved, time & confirm function added
2022-05-08 confirm button light and sound signalisation added
2022-05-09 open button bug fix
    [simple_platform_dev.ino]
2022-05-11 ALU profile box added
    [888_2001.scad, complete.scad, cube_box.scad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]
2022-06-23 cube_box adjustments
    [complete.scad, cube_box.scad, parameters.scad]
2022-06-23 Blade holder parts
    [888_3004.scad, 888_3005.scad, 888_3006.scad]
2022-06-23 STP cable holder
    [888_2002.scad, 888_2002_printplate.scad, 888_2003.scad]
2022-06-23 Locking mechanism progress
    [888_3001.scad, 888_3002.scad, 888_3003.scad]
2022-06-23 888_3004 add printplate state
    [888_3004.scad]
2022-06-23 assemblies fixed added rotor_lock.scad
    [888_2002.scad, cube_box.scad, lock.scad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]
2022-06-23 animated rotor_lock
    [888_3001.scad, lock.scad, rotor_lock.scad]
2022-06-23 Complete scad fix
    [complete.scad]
2022-07-11 Rotor lock functional form
    [888_3001.scad, 888_3001_printplate.scad, 888_3002.scad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]
2022-07-16 add platform holder
    [beam_holder.scad, beam_holder.stl]
2022-07-28 Starting platform tilted
    [888_2004.scad, 888_2004_printplate.scad, beam_holder.scad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]
2022-07-28 New teeth for lock
    [888_1005.scad]
2022-08-16 Servo lib fix
    [rotor_lock.scad]
2022-08-16 Lock getting new servo
    [888_1008.scad, lock.scad, parameters.scad]
2022-08-17 Lock tooth tilted
    [888_1005.scad, 888_1005_A_printplate.scad, 888_1005_B_printplate.scad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]
2022-08-17 Angle problem bug fix
    [888_1005.scad]
2022-08-17 Update trigger switch documentation.
2022-08-17 Add trigger switch photo.
2022-08-17 Rotor lock gears added
    [888_1002.scad, 888_3002.scad, 888_3002_A_printplate.scad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]
2022-08-17 Screw diameter adjusment
    [parameters.scad]
2022-08-17 888_3003 servo hole hot fix
    [888_3003.scad]
2022-08-17 Lock tolerance fix
    [888_1006.scad]
2022-08-17 Brush length and density fix
    [888_3004.scad]
2022-08-17 Adding prinplate for 888_3004-3006
    [888_3004.scad, 888_3004_printplate.scad, 888_3005_printplate.scad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]
2022-08-17 Lock main arm gap fix
    [888_1005.scad]
2022-08-17 Main holder done
    [888_3001.scad, 888_3001_printplate.scad, rotor_lock.scad]
2022-08-17 Assemblies rewrite
    [complete.scad, cube_box.scad, front_support.scad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]
2022-08-22 New platform mounting mechanism added
    [888_2005.scad, 888_2005_printplate.scad, cube_box.scad]
2022-08-23 Ground station scheme added
    [ground_station.bom.tsv]
2022-09-04 tolerance fix
    [888_1006.scad]
2022-09-09 Platform scheme
    [platform.bom.tsv]
2023-01-16 Add makefiles and printer configs pointing to slic3r. Block uploading builded files in .gitignore, set default profile to all printplates
    parts 1005,1008,3001,3002B,3004,3005/6 need to setup correct supports
    [888_1001_printplate.scad, 888_1002_printplate.scad, 888_1003_printplate.scad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]
2023-01-16 fix multiple mainfold error
    [888_3005.scad, 888_3006.scad]
2023-01-16 Fix multipe mainfold in 3001.
    [888_3001.scad, 888_3005.scad]
2023-01-16 make part 3001 smooter
    [888_3001.scad]
2023-02-28 slice 100x parts using prusa slicer with default config
    [888_1001_printplate.scad, 888_1002_printplate.scad, 888_1003_1004_1006_1007_1009_printplate.scad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]
2023-02-28 update printer configs
2023-03-01 Add 200x parts - fix printplates
    [888_2002_printplate.scad, 888_2004.scad, 888_2004_printplate.scad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]
2023-03-01 add combined 200x printplate
    [888_2004_2005_printplate.scad]
2023-03-02 Add 3000 group, try to fix some printing problems, add combinet print plates
    [888_3001.scad, 888_3001_printplate.scad, 888_3002_AB_3003_printplate.scad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]
2023-03-09 update printer settings
    [888_4000_Test_printplate.scad]
2023-03-09 add some cleance to alu profile, central bearing and switch few contatnts to M3 settings
    [888_1004.scad, 888_2004.scad, 888_2005.scad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]
2023-03-10 rework part 1004.
    [888_1004.scad]
2023-03-10 use less density supports, fix 1004
    [888_1004.scad]
2023-03-10 fix 1004, add necks instead of using 1007
    [888_1003_1004_1006_1007_1009_printplate.scad, 888_1004.scad, 888_1006.scad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]
2023-03-16 print 4x 1007 under lock servo
    [888_1007_printplate.scad]
2023-03-16 Add distancers for rotor lock ax
    [888_3007.scad, 888_3007_printplate.scad]
